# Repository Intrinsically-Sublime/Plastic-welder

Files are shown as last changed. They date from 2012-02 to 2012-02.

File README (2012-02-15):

---Description---

WARNING handle with caution. Keep away from children, pets and anything flammable. USE WITH CARE. I will not be held responsible for injuries or damages from the use of this device

The electronics are the work in progress.

(low duty cycle only)

With the limited build size of most 3D printers I found a need for a better way to assemble multi-piece models and the obvious choice seemed to be a welder.

It based on Gregs hinged accessible extruder (wildseye hotend version).
It uses my revision of Ryhs_jones Herringbone gears.
thingiverse.com/thing:10538

Universal mount for miscellaneous gear motors or steppers.

Uses 70mm of 1/2" PTFE rod.

The heater barrel is a 1/4" bolt drilled to 3.5mm.
Aluminium heater block with 6.8ohm vitreous enamel resistor heater.
100k thermistor.
1/4" brass acorn nut with .8mm nozzle hole.
Built the same way as geometricobjectdepositiontool.blogspot.com/p/no-lathe-plumstruder.html but with out any support material.
( I did not feel it needed support because it is to be used hotter and slower which equals lower pressures, as well as for shorter durations )

The heater circuit I used is similar to pdf417.blogspot.com/2010/09/problem-with-extruder-heater-solved.html but used components I had lying around.

The gear box I used was from some old toy.
(My_gearbox.stl is a block model of the gearbox I used. I created the model to be sure it would fit. Do NOT print it unless you want to compare it to one you have)

Electronics
PLEASE use the circuit mentioned earlier pdf417.blogspot.com/2010/09/problem-with-extruder-heater-solved.html unless you are like me and have a lot of low power mosfets.

The Eagle file provided is for my heater circuit and is still undergoing testing.

I have 100 TIP29's around so have made use of them here. They are only rated to 1A continuous 3A peak each so I have used three of them in parallel.

T1 = PNP transistor (to turn off the three NPN's when at set temp)(must be capable of R4's current flow)

T2-T3-T4 = NPN transistors (3A total minimum)

L.E.D. 1 = (turns off when at set temp)

R1 = 100k ntc Thermistor (measures temp)

R2 = 50K pot (sets temperature)

R3 = 1k 1/8w resistor (for L.E.D.)

R4 = based on gain of transistors used (holds T2-T3-T4 high)(I choose 1/2watt 150ohm resistor @ 12V = 80mA * 40 (TIP29 = 40x gain) = 3.2A max output)

R5 = 5K 1/8w resistor (increases adjustability at higher temps)

C1 = Smoothing cap rated higher voltage than 12V and as high of capacity as you have lying around and still fits on the board (8mm dia max)

All modelling done with Blender 2.57 

---Instructions---

I printed the entire thing in PLA and the handle does get soft near the end after a few minutes. If you have the ability to print in ABS I highly recommend printing the handle in ABS.

Print
1 main body
1 idler
1 handle
1 large gear and 1 small gear
You can still use Gregs original Gears or the herringbone ones.
The Gear named Plastic Welder Small Gear is designed to it on a 5.5mm hex shaft.

Assemble extruder portion as per Gregs extruder.

If using a small DC motor you may need to use a custom small gear.

If using DC motor drill holes for mounting and screw down.

If using Stepper attach using four holes provided.

Build your favourite hotend using 1/2" PTFE (PTFE 70mm's fits inside the handle and body)

Install prepared PTFE in body using two screws through mounting holes in the body) (groove mount style)

Slide handle over PTFE rod and tab on body. (install bolt through hole provided if necessary)

Install hotend in PTFE.

Wire Hotend to Heater control board.
pdf417.blogspot.com/2010/09/problem-with-extruder-heater-solved.html
Or the one I provided
Or your RepRap electronics
Or ?????

Wire DC with a PWM circuit such as dprg.org/tutorials/2005-11a/index.html
Or direct through a switch
Or ?????

Wire Stepper motor using a microcontroller and Stepper driver
Or use your RepRap electronics
or ?????

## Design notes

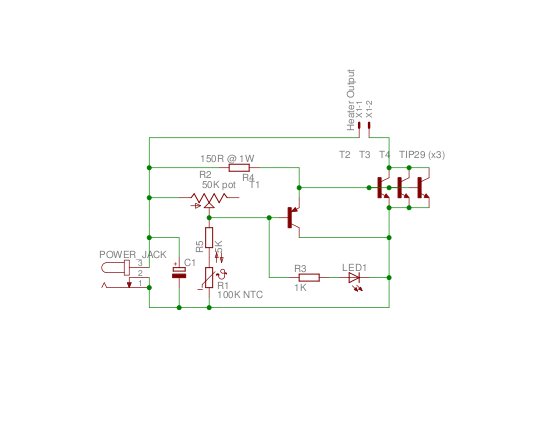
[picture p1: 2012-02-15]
Plastic_welder_heater-3.1.JPG

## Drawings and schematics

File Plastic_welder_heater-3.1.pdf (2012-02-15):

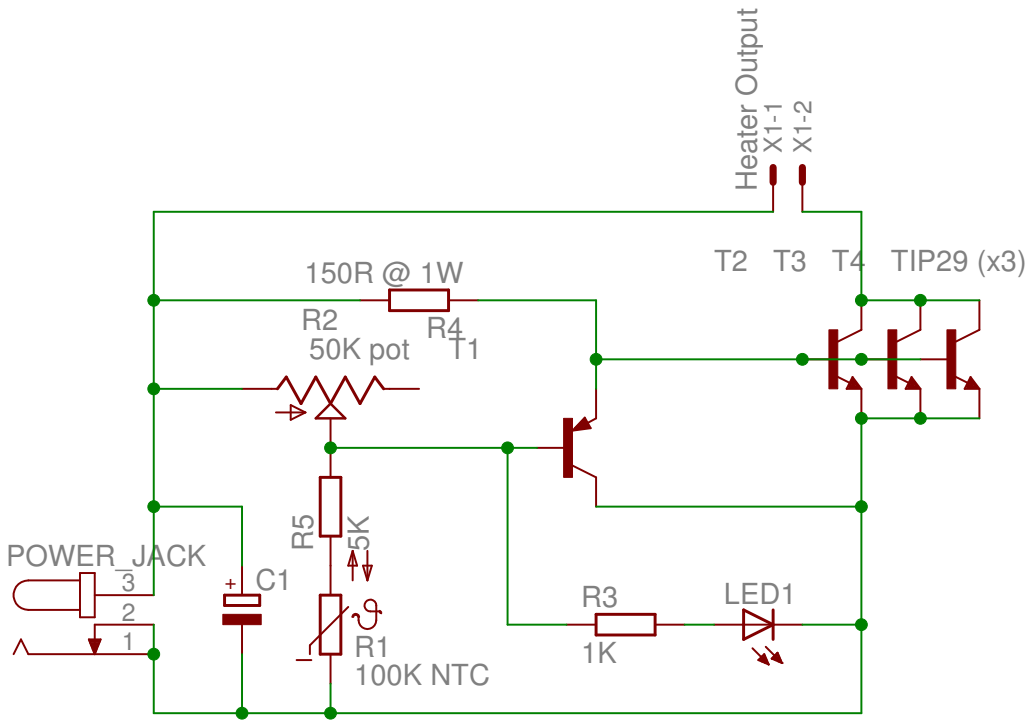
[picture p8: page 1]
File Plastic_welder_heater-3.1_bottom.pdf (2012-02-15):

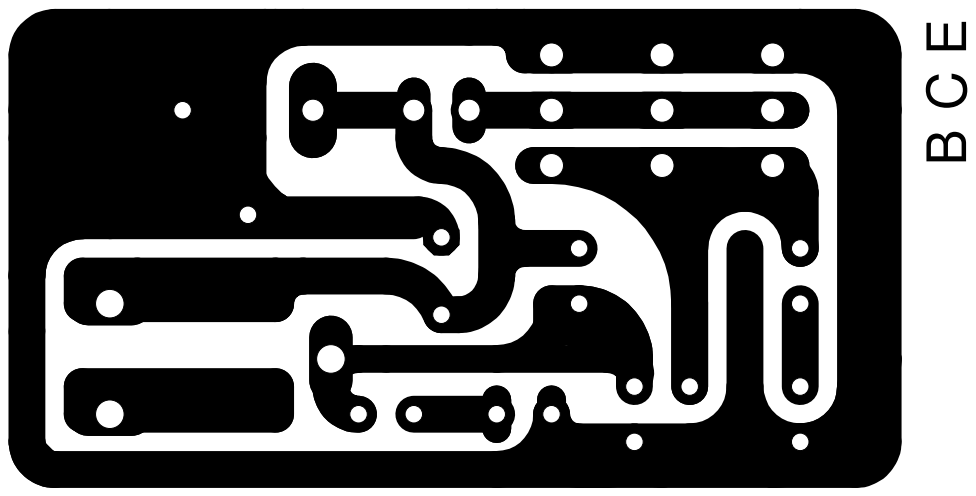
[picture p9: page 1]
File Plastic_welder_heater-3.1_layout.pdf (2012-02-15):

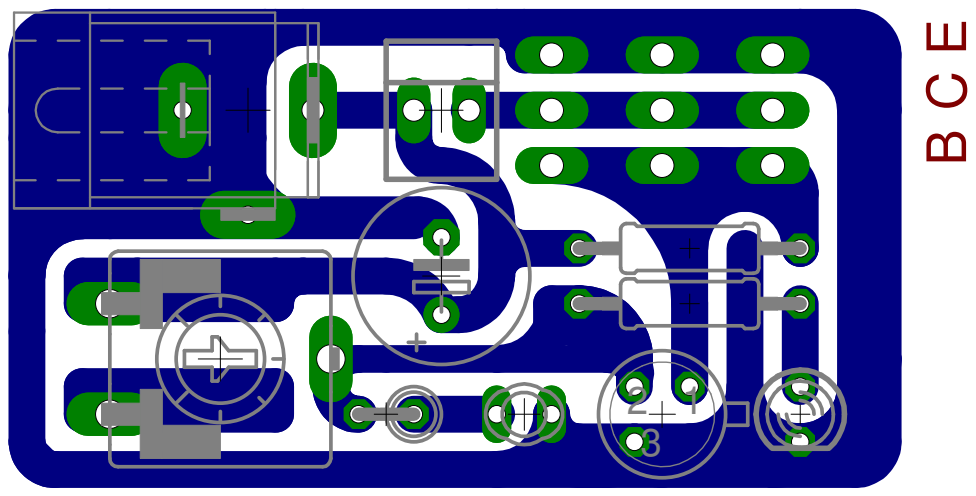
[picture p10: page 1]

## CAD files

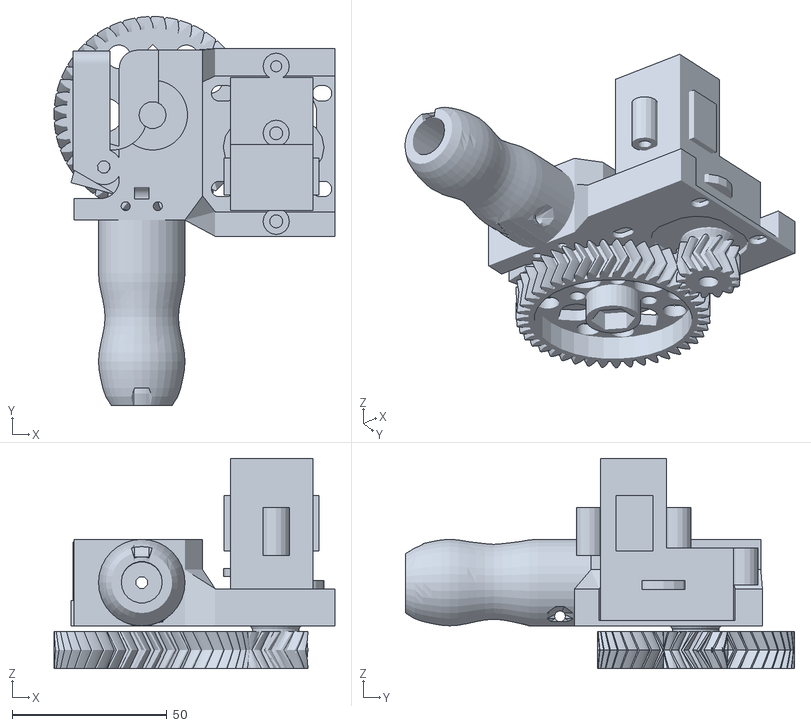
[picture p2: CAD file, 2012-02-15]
Plastic_welder.stl
90.9 x 125.9 x 68.1

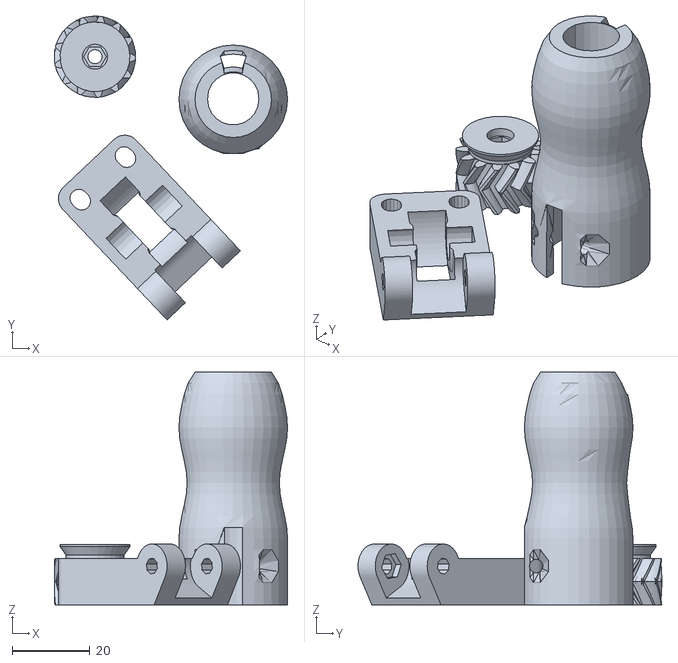
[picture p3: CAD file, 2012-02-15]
sheet.stl
60.1 x 78.3 x 60.0

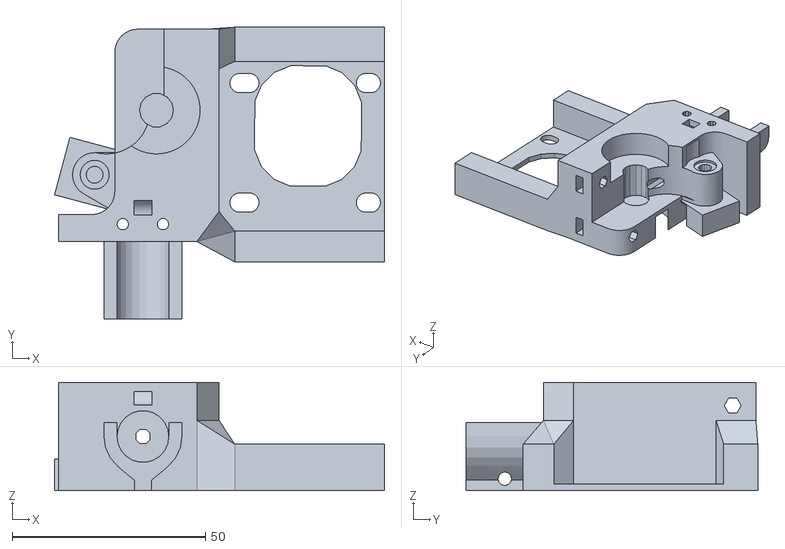
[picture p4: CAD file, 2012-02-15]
Plastic_welder_body.stl
85.4 x 75.5 x 28.0

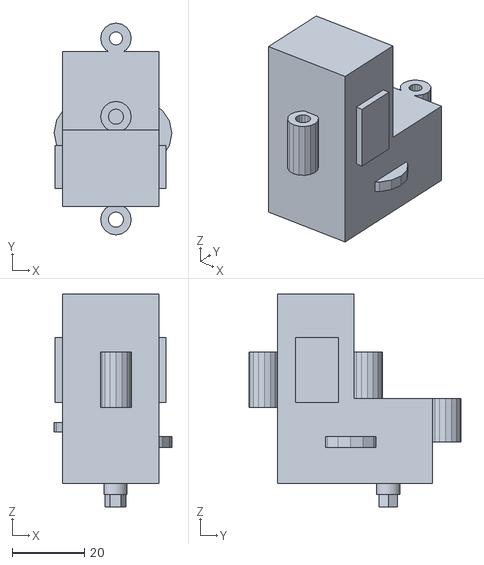
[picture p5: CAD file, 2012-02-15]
My_gearbox.stl
32.6 x 58.7 x 59.0

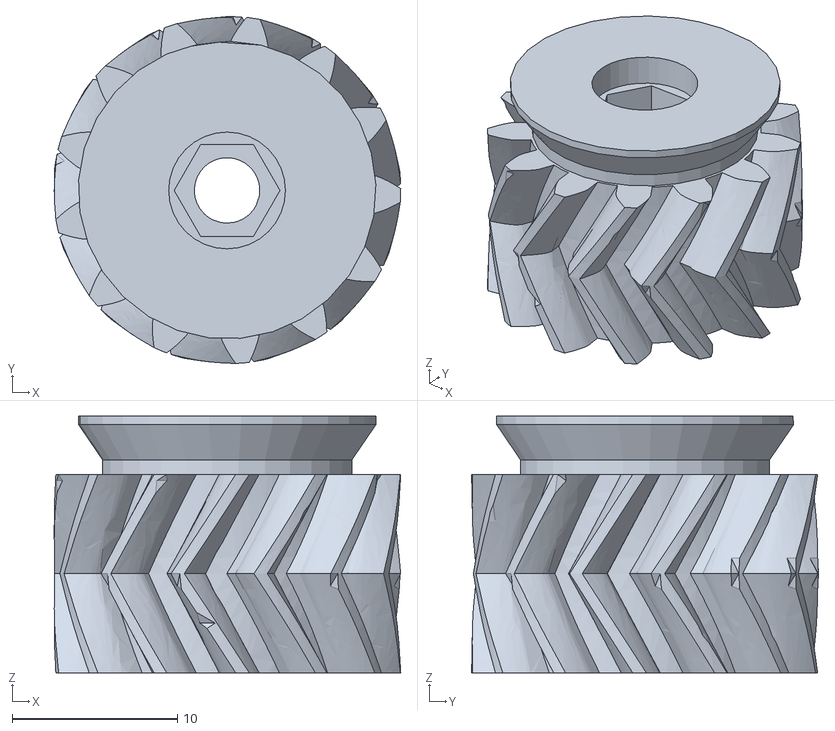
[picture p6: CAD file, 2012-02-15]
Plastic_welder_small_gear.stl
21.0 x 21.0 x 15.5

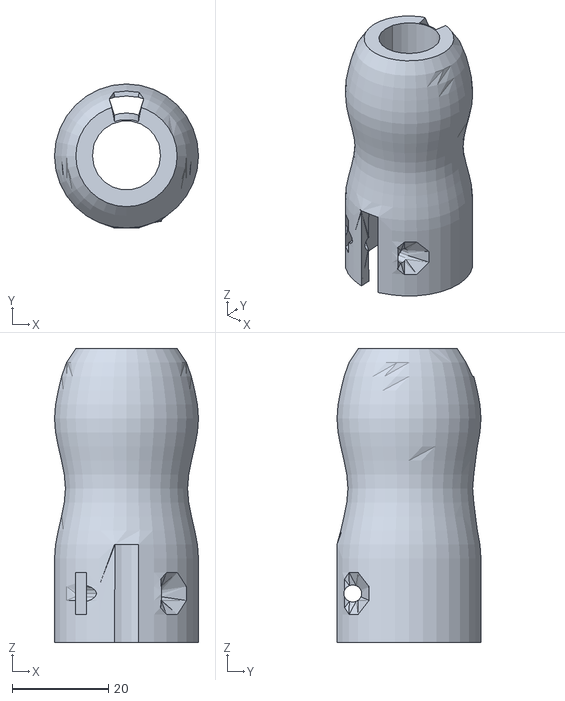
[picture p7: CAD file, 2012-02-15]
Plastic_welder_handle.stl
30.0 x 30.0 x 61.2

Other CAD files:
Plastic_welder.blend
